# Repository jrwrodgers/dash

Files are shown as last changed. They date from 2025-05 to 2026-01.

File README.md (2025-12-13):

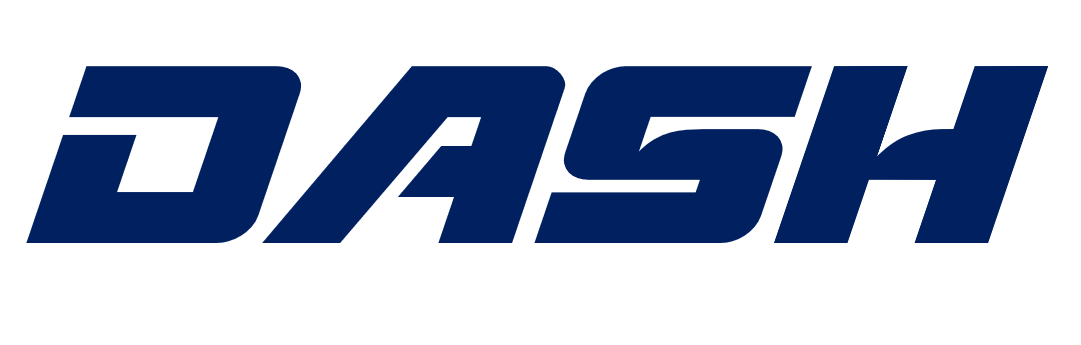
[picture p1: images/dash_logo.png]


The aim of this frame design was to create something:
 - Opensource so that the community benefits both in shared design improvements but also in availability and cost through multiple manufacturing paths.
 - 20x20mm compatible.
 - Some extra space to allow all ESC types to fit. A little extra body width and standoff spacing is a small cost for wider compatibility.
 - Strong enough to survive a few hard crashes yet still flies well enough to be comptitive at the cost of a few grams. More flying = flying faster!
 - The arms are boomerang since this stiffness improvement and hence handling were considered more important than changing a few extra bolts and reduced strength in the overall design.
 - A focus has been made on increasing arm and mid plate stiffness through weave orientation and configuration. Stiffer frames move the resonances to higher frequencies allowing less filtering, improved flight performance both in stick following and prop wash.

Version History [here](./versions.md)
  
Specs:
- Motor to Motor Left Right = 132.1 mm
- Motor to Motor Front Back = 156.1 mm
- Motor to Motor Diagonal = 204.5 mm
- Standoff Spacing Left Right = 24 mm
- Standoff Spacing Front Back = 48 mm
- Battery Strap Width = 20 mm
- Arm Thickness = 6mm
- Arm Angle = 90 deg
- Mid Plate Width = 34 mm
- Motor Mount Diagonal = 16 mm (22xx motors)
- Weight (Including hardware) = 81g

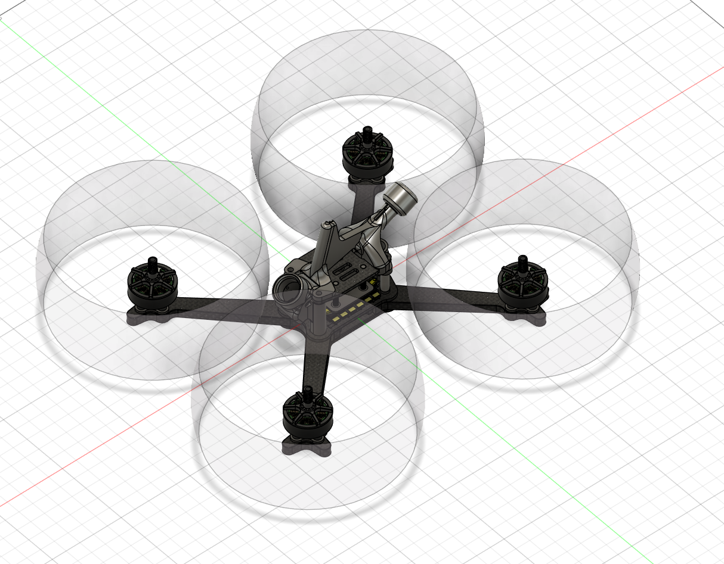
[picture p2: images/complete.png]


<!--![image](images/frame.png)

#![image](images/frame_above.png)

#![image](images/20250630_115858.jpg)

#![image](images/20250630_115844.jpg)
-->

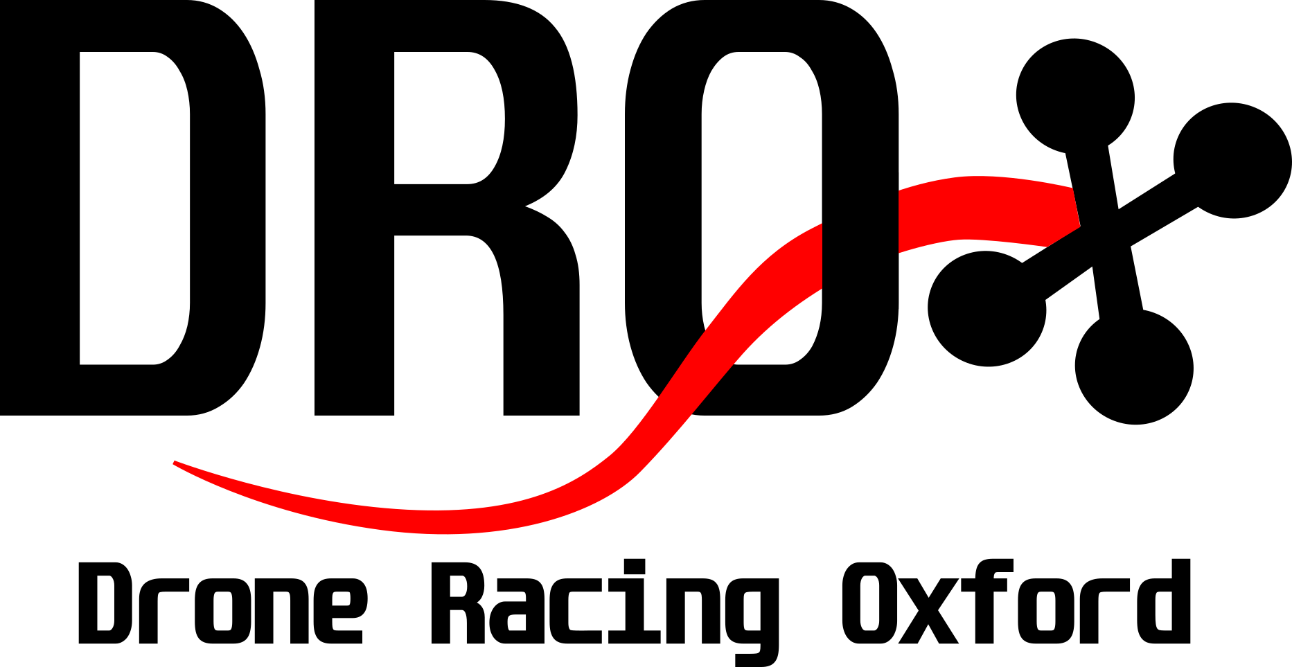
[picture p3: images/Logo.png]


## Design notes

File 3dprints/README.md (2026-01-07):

3D prints to fit the frame

- Camera Mount, Nano90V2 55deg , also with parametric fixed angle in Fusion360 model
- Horn and Antenna Mount
- Pigtail plate
- Stack nuggins
- Motor spacers
- Battery Docking Pad

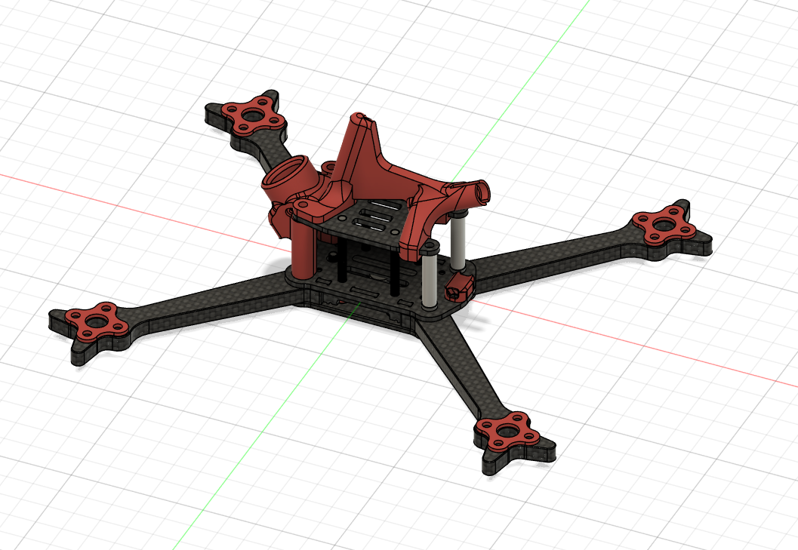
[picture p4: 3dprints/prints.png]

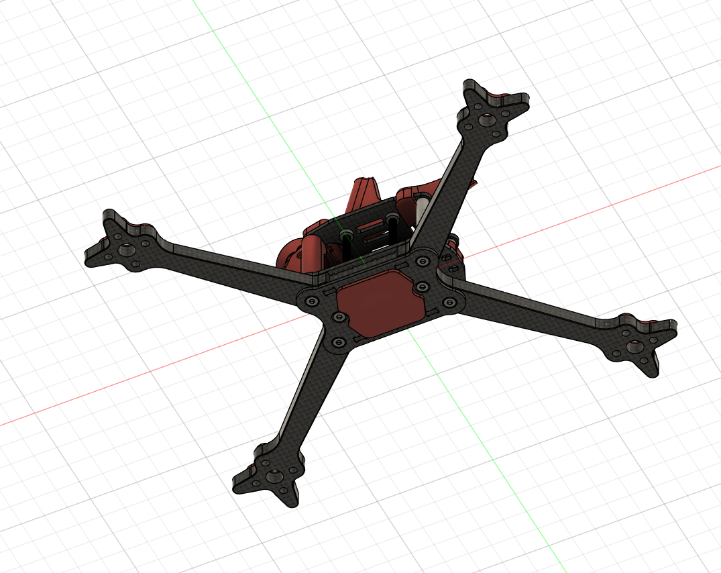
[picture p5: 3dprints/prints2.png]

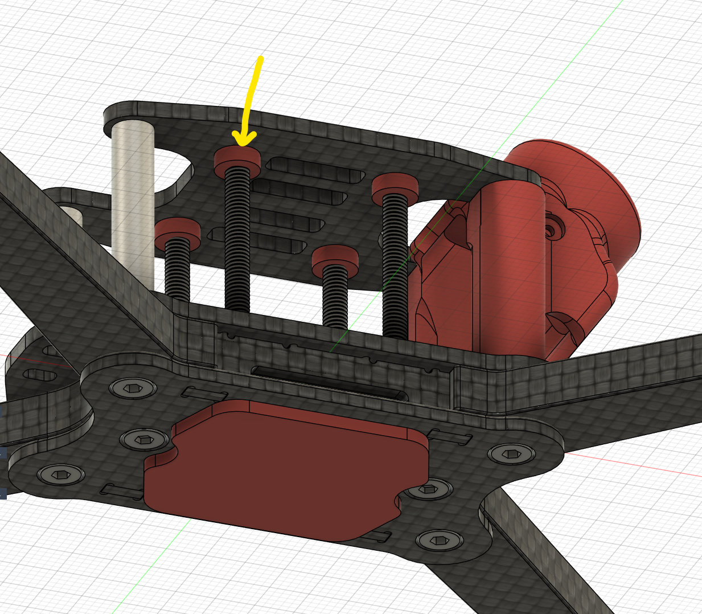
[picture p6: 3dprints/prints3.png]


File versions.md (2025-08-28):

Version 1

- Initial release of the frame
- Arms regular failures from torsional delamination
- Some arm bending modes needed the filters to be set up carefully

Version 2

- Arm width increased and made more uniform along length, arm V web radius increased 
- Arm V-angle changed to be pure 90 degs to orientate fibres with T700 weave NB - this is now a stretch X frame and will require different pitch and roll tuning. Rear motors should have cleaner air with extra proximity to the front motor wakes.
- Mid plate now has pigtail cable tie holes for strain relief
- Battery Strap width limited to 20mm width to increase mid plate sandwich torsional stiffness
- VTX is has no fixings but is held on stack with tpu nubs on underside of top plate
- Aerial and Fin print is designed for a Rush Cherry 2
- Only one arm failure so far outbord.

Version 3

- Due to the much increased strength and stiffness of the V2 the arms have been made narrower for weight saving
- Stacks have been lozenged a few times so moving to high tensile steel for the stand off bolts
- Mid plate includes fixing holes for Gorilla Mounting ESC
- Bottom plate includes holes for stack bolt access and also to act as a docking pattern for battery pads
- Chassis weight (all hardware is estimate to be ~72g - 16% reduction from V2

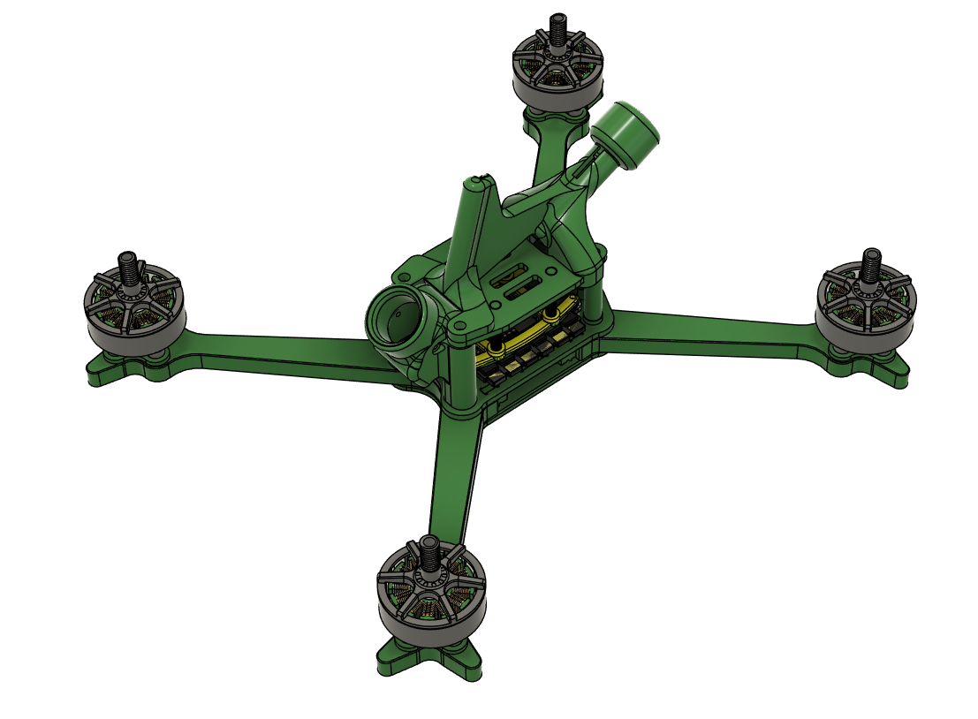
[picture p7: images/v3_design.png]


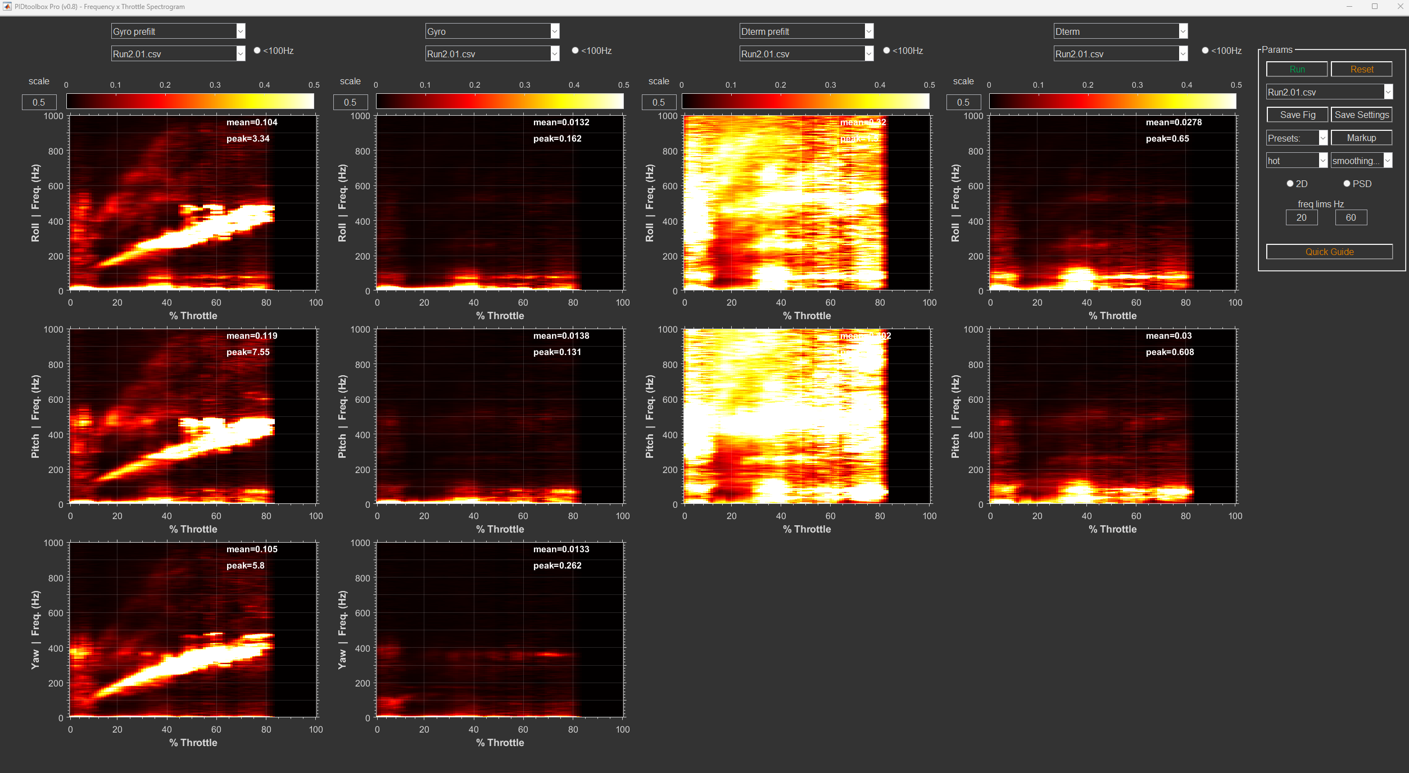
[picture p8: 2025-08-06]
images/PIDTB_spectrum2.png

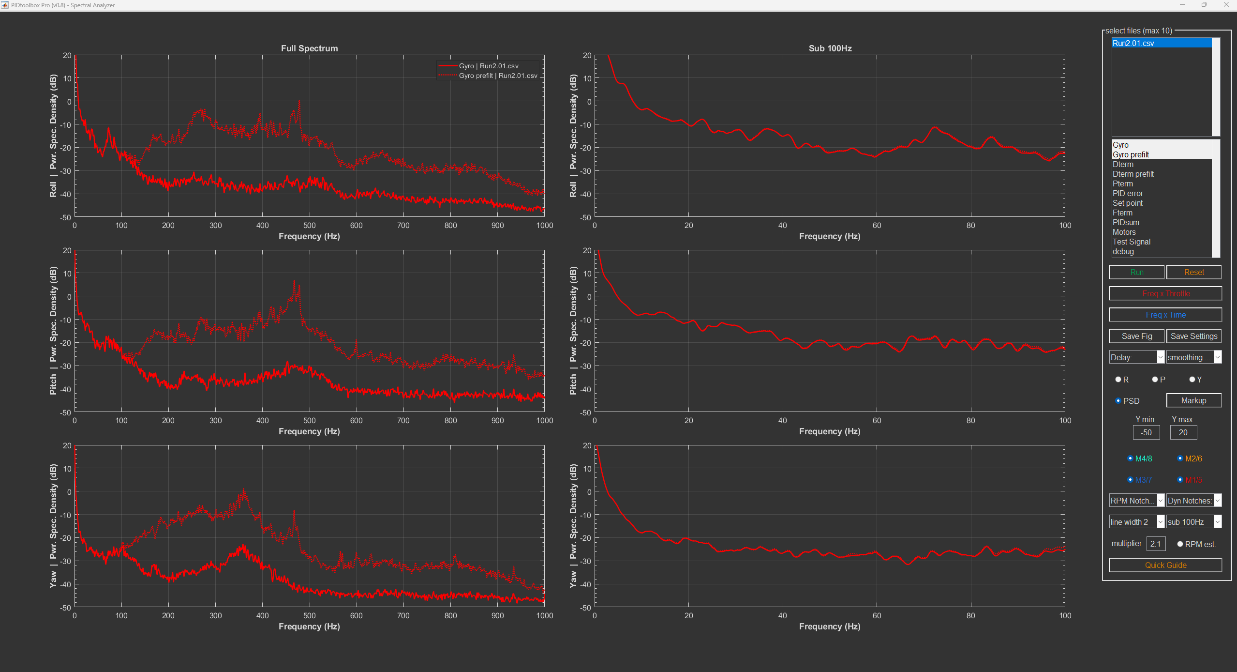
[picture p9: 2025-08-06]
images/PIDTB_spectrum1.png

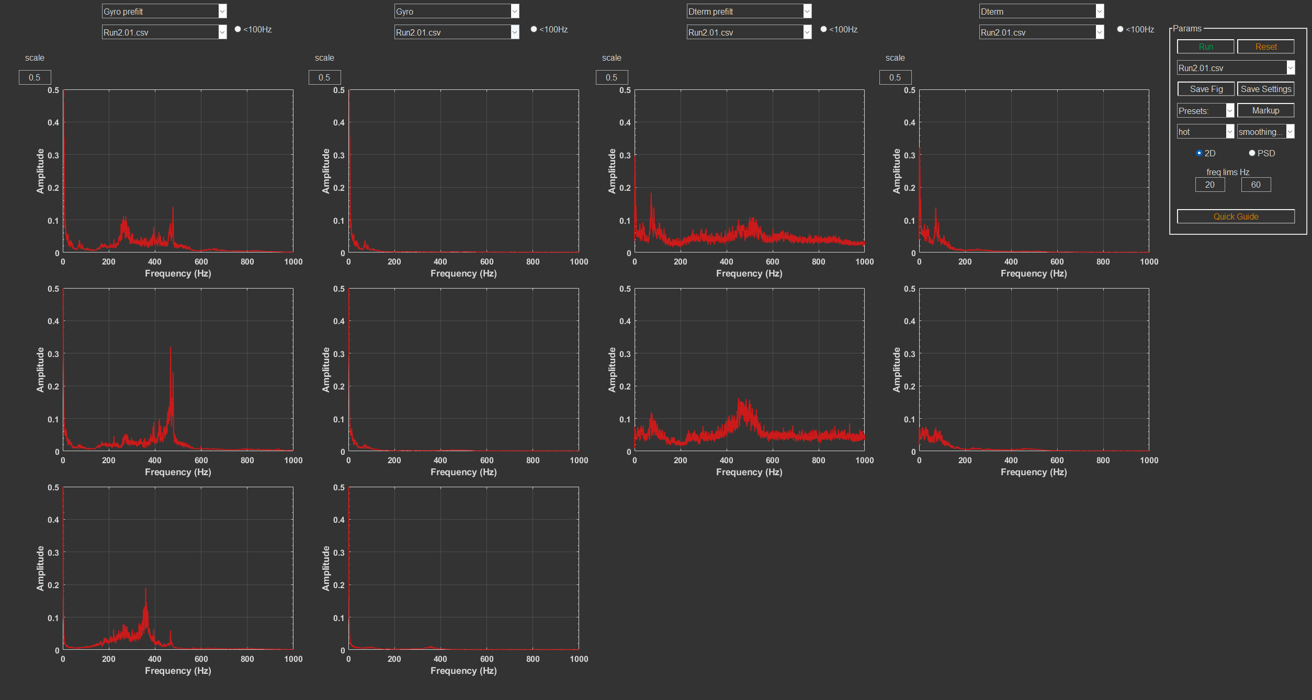
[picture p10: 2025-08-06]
images/PIDTB_spectrum3.png

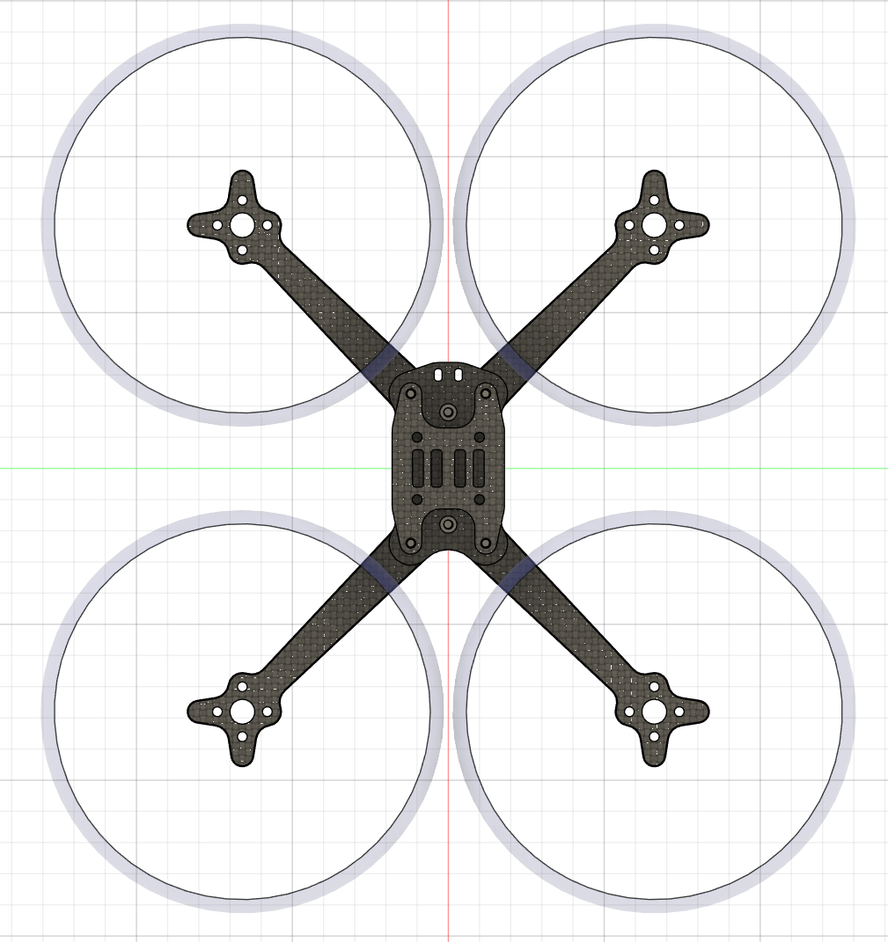
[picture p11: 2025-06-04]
images/frame_above.png

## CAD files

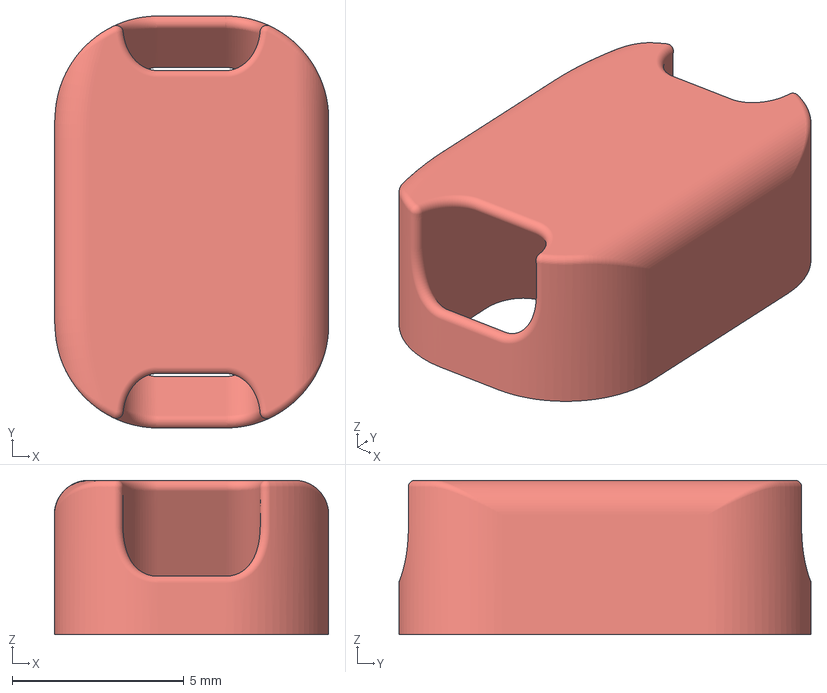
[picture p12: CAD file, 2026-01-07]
3dprints/Pigtail Plate.3mf
7.99 x 12.0 x 4.50 mm

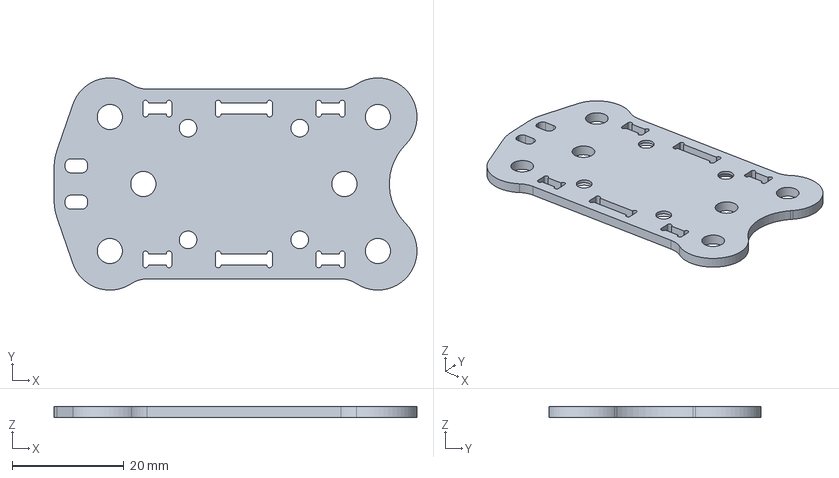
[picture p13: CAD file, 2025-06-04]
parts/mid_plate.step
65.0 x 38.0 x 2.00 mm

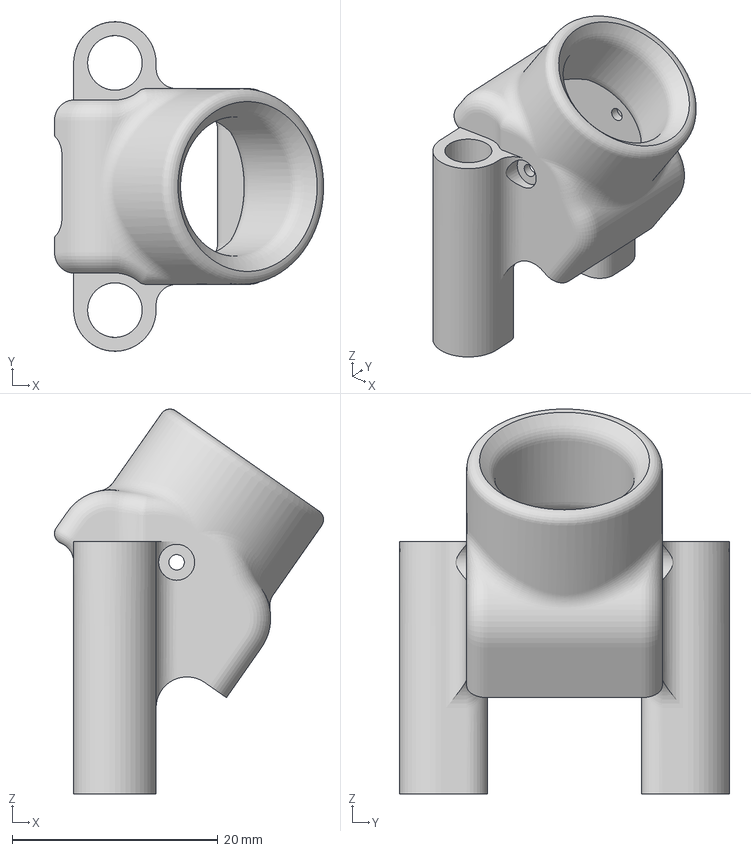
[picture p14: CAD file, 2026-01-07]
3dprints/Nano90 Camera Mount.3mf
26.1 x 32.0 x 37.4 mm

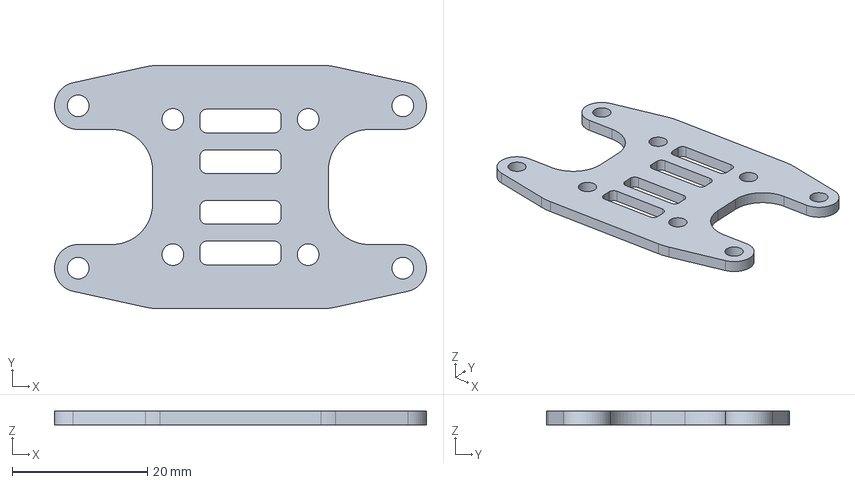
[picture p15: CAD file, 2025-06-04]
parts/top_plate.step
55.0 x 36.0 x 2.00 mm
Mid Plate
Top-Plate

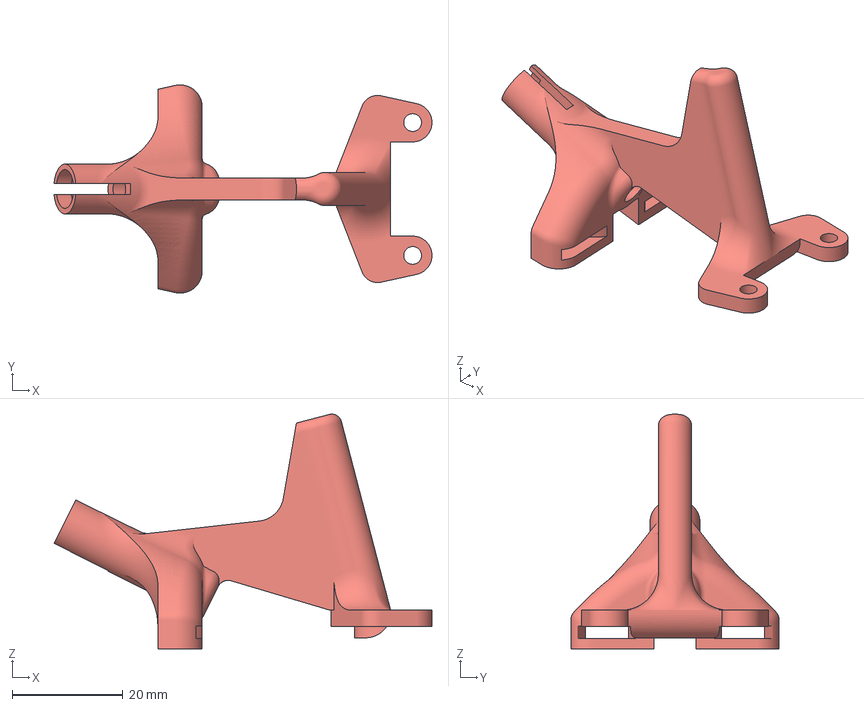
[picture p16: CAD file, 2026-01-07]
3dprints/Turtle Horn.3mf
68.3 x 37.6 x 42.4 mm

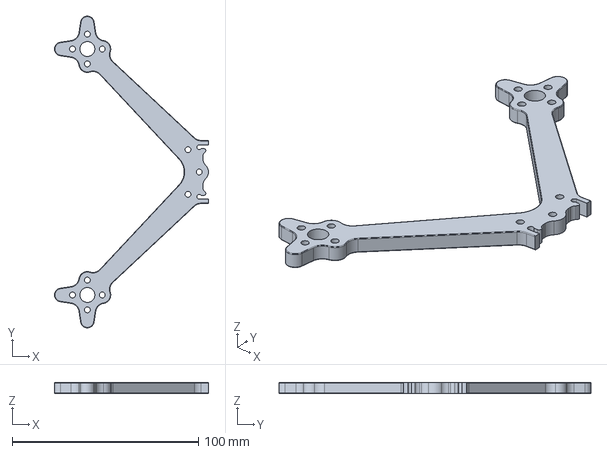
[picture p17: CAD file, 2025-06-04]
parts/arm.step
82.7 x 167.4 x 6.00 mm

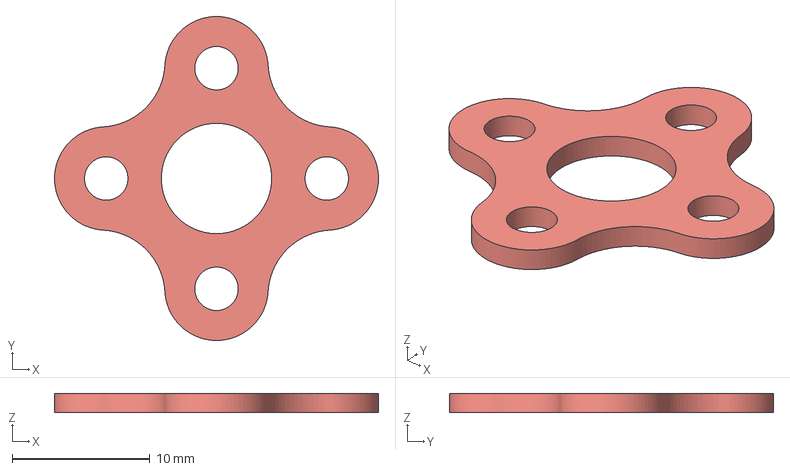
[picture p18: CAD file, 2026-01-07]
3dprints/Motor Spacer.3mf
23.5 x 23.5 x 1.40 mm

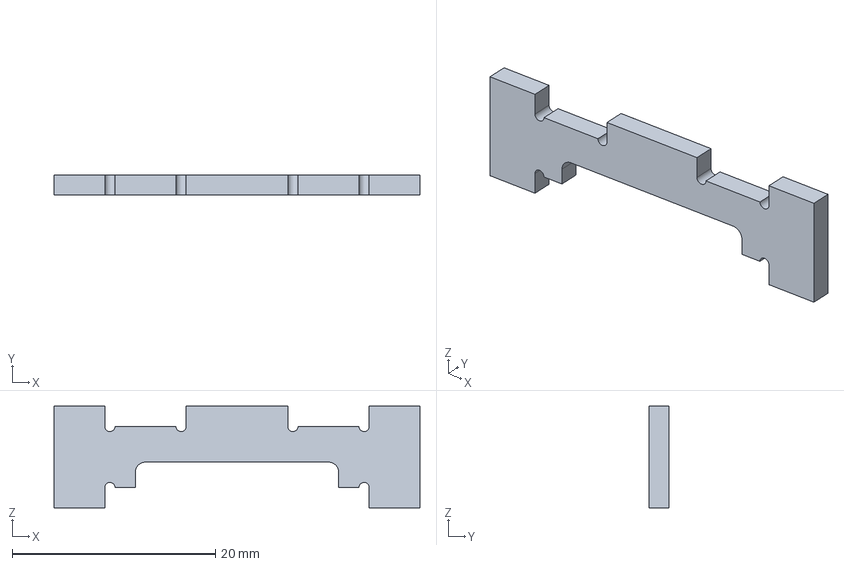
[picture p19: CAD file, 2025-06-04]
parts/rib.step
36.0 x 2.00 x 10.0 mm
Mid Plate
Rib

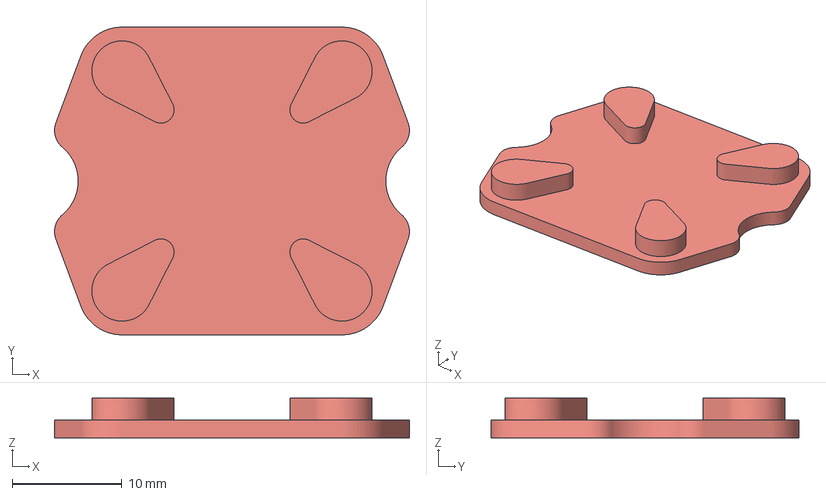
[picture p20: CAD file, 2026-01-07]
3dprints/Battery Dock.3mf
32.3 x 28.0 x 3.60 mm

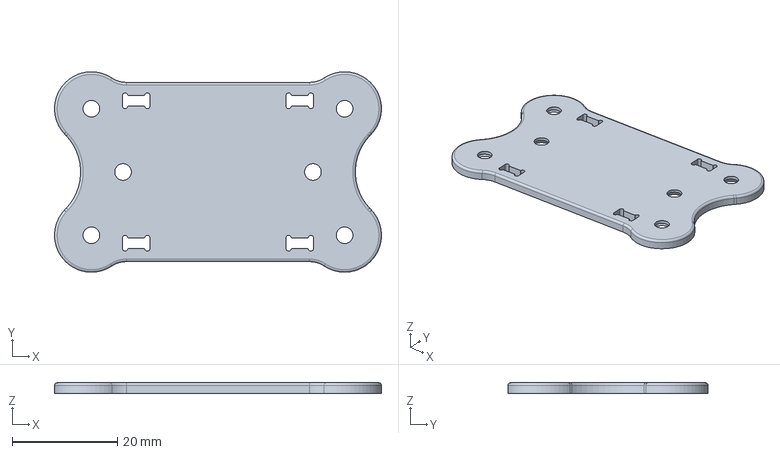
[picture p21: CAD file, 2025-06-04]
parts/bottom_plate.step
62.0 x 38.0 x 2.00 mm

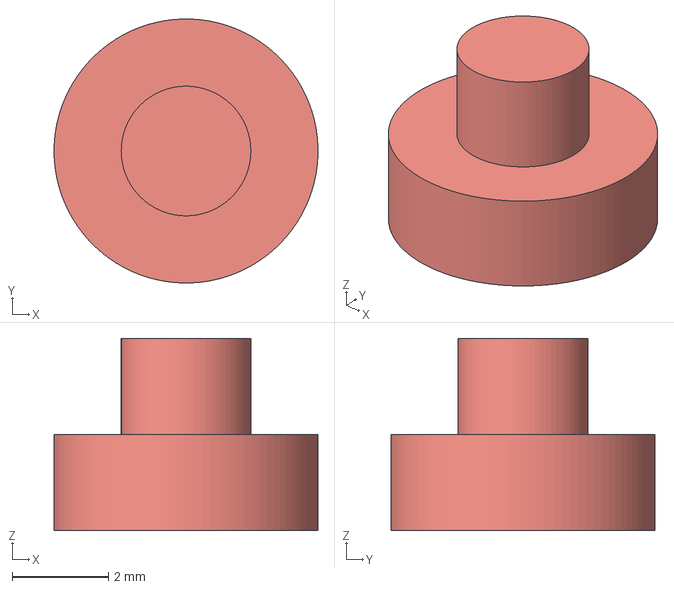
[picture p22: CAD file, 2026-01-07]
3dprints/Stack nuggin.3mf
5.50 x 5.50 x 4.00 mm

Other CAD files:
3dprints/Nano90 Camera Mount.f3d
parts/arm.stl
parts/bottom_plate.stl
parts/mid_plate.stl
parts/rib.stl
parts/top_plate.stl

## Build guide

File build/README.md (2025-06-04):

M3 Press Nuts are used in the mid plate

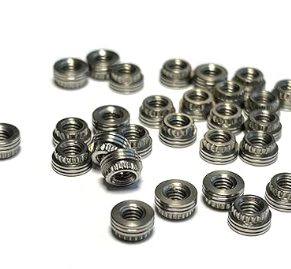
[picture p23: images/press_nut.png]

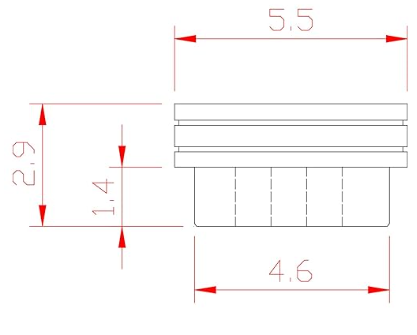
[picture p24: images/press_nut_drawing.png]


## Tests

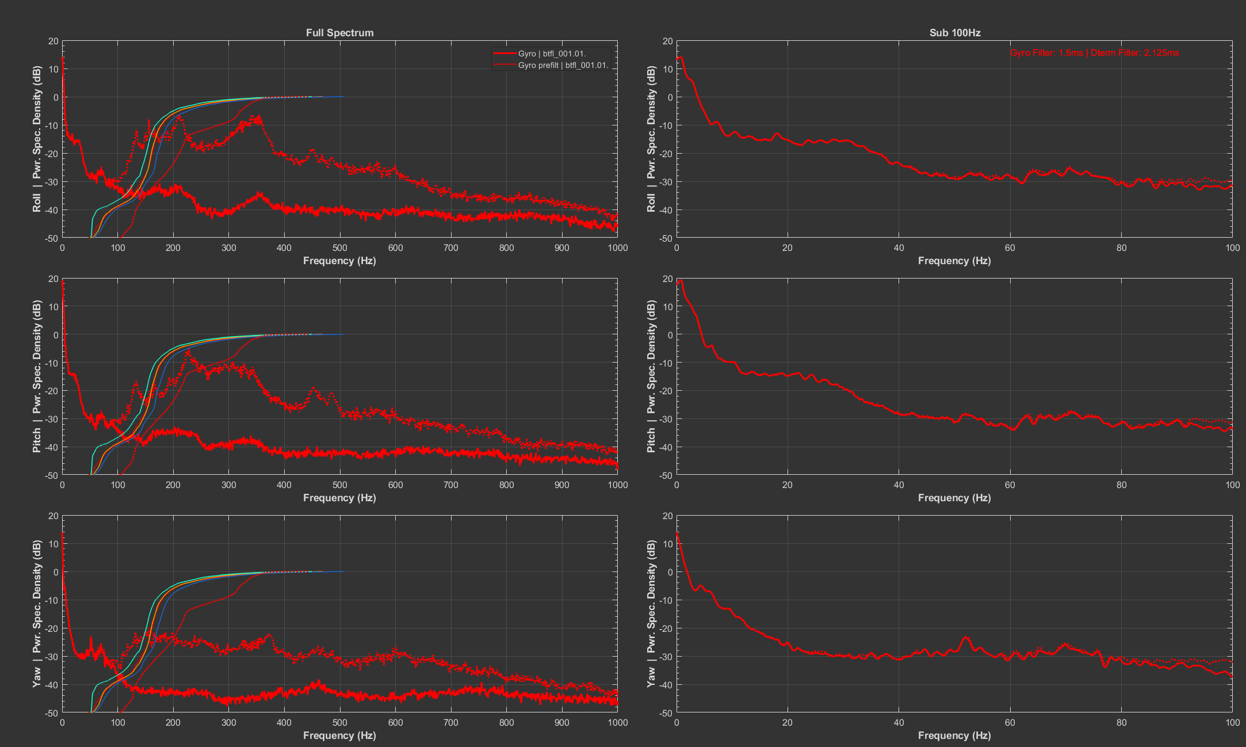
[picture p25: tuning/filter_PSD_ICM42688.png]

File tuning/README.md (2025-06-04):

This will be some notes regarding filter tuning for the frame.

Initial results on the ICM42688 gyro
